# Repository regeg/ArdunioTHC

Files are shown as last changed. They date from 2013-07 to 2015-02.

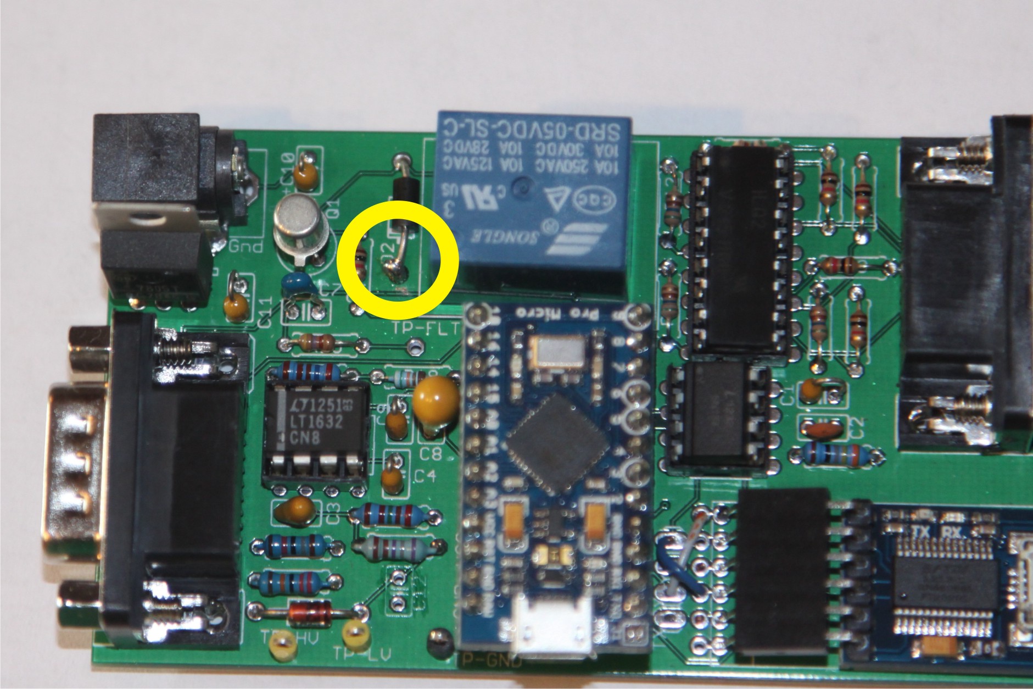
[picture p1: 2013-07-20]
THC Manual/THC Manual/RevE-M top solder bridge.jpg

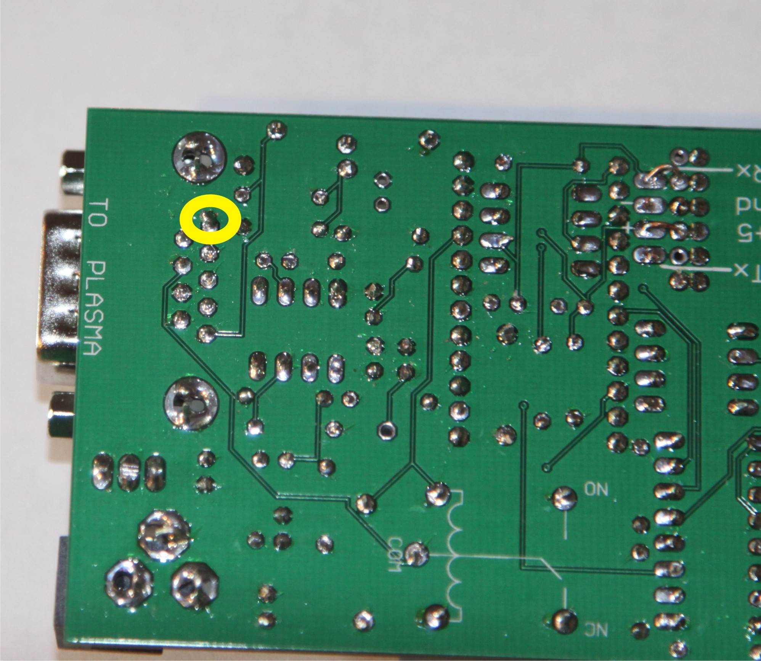
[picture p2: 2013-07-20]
THC Manual/THC Manual/RevE-M bottom Solder Bridge..jpg

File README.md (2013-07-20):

ArdunioTHC
==========

Arduino-based Torch Height Controller for CNC Plasma torch systems

(see "Status.txt" for current project status.)

***

WARNING: CNC systems are inherently dangerous.  Use of this hardware and software is at your own risk.  I am not an expert at CNC systems, THC's or electrical design.  I'm just an embedded software guy who did the hardware design with help from some experienced EE's.

When working with a THC, you're messing with high voltage.  All of the project information is only for use with the acknowledgement and agreement that no statement of safety or appropriateness is offered for any of the information.  Additionally, you take full responsibility for all uses of this hardware, software and documentation.

***

Background
----------
Having recently built a Computer Numeric Control (CNC) driven Plasma torch cutting table, I wanted to add a torch height controller (THC).  I decided to make my own and open source it.

Both the CNC table build and the THC development couldn't have been done without the significant support I received from the folks on the Everlast Forums.  	www.everlastgenerators.com/forums
These are great forums for support with all things welding and plasma cutting.

I have built this THC specifically to work with the Everlast Power Plasma 50 plasma torch.  This is the unit I have and I've been very happy with it.

There are two very significant aspects that make the Everlast PP50 ideal for this project.  They are:
	- Pilot Arc start
	- full CNC interface

Pilot Arc Start - the PP50 offers a "pilot arc" start, this is in contrast to an HF (High Frequency) start.  The HF start is very noisy and has been reported to cause significant interference with computer systems.

Full CNC Interface - all control signals are available on a connector on the back of the PP50.  They are:
	- Torch On (input, dry contact)
	- Arc Good (output, dry contract)
	- Full torch voltage
	- Divided torch voltage

This hardware design uses the full arc voltage.  I've observed about 2 volts of noise on the torch voltage signal, no matter what you use (full voltage or divided voltage).  By using the full voltage and dividing it myself, the noise is kept to a significantly lower percentage of the signal.

I have not tested the THC with any other brand of plasma torch.  It should be a good starting point to make a THC to work with other torches that provide a CNC interface.

Hardware
--------
There are two versions of the shield.  The first is a shield and will work with an Arduino Mega.  This has been the primary platform.  A newly released version uses the Arduino Micro Pro.

The hardware provides:
	- isolated interface to CNC system
	- interface to Power Plasma 50 CNC interface
	- isolated RS-232 (TTL levels) for interface to THC

--

I will be updating all files as the project progresses.  There will be the following subdirectories:
	- "ArduinoSource", using Eclipse plugin from www.baeyens.it/eclipse/
	- "THC Manaul", a users guide to building and use the THC
	- "HardwareDesign", Eagle schematic and PCB layout files
	- "WindowsSource", C# .Net application used to capture cutting data
	- "Mach Plugin", A Mach3 plugin to allow Mach to control the THC

License
-------
This is copyrighted software that is released under the Creative Commons Attribution-NonCommercial-ShareAlike 3.0 license

The unofficial summary is:

You can use it as it is for non-commercial purposes.  If you modify it, you must make the modifications public and attribute the original source to me.

(If you want to license it for commerical use, please contact me.)

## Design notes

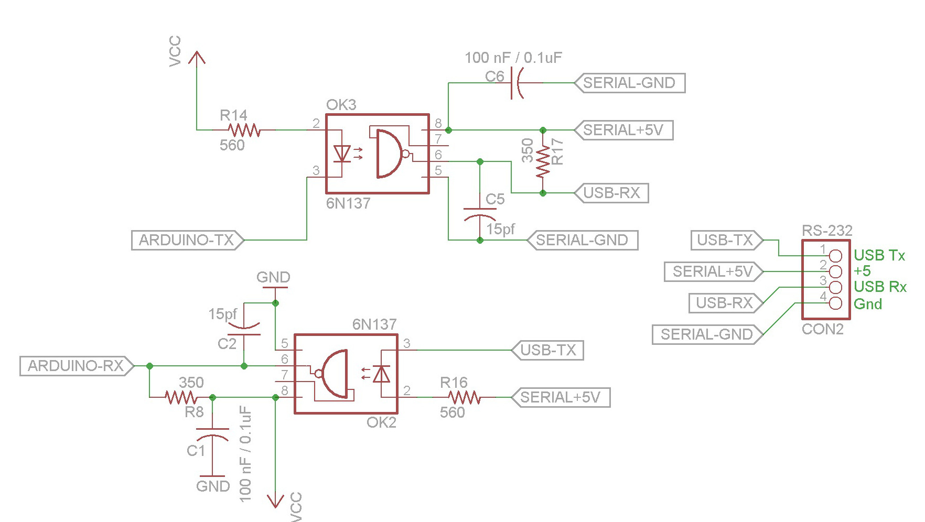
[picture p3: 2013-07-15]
THC Manual/THC Manual/RS-232Schematic.jpg

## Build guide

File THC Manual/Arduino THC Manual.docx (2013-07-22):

For the Everlast Power Plasma 50

User Manual

Open source hardware and software free to non-commercial use.

www.github.com, project: regeg/ArduinoTHC

Revision | Date | Changes
0.1 | 7/11/13 | Initial version w/ pictures and both Shield & Micro
0.2 | 7/20/13 | Added BOM and white wire directions for Micro board
0.3 | 7/22/13 | Added section on programming the Arduino

| This icon denotes a significant piece of information.

| This icon denotes a very important warning.

# 1. CNC/Plasma System Requirements

This THC system was designed with specific requirements in mind. The target requirements are:

- Everlast Power Plasma 50 (PP50) plasma cutter
- Mach3 CNC Driver, licensed version required for THC use

## Everlast Power Plasma 50

The PP50 was selected as the initial plasma system to be supported for two reasons:

- It is a good performing and economical plasma cutter with a CNC port and a pilot arc start
- It’s the cutter I have

One aspect of the PP50 CNC interface is that it includes a 100K ohm resistor on both the + and – poles of the arc voltage signal. This plays a role in determining the voltage divider resistor values. While this THC uses undivided voltage, it is not recommended that it be connected directly to the torch voltages (if the plasma unit has no CNC interface). This would require hardware design changes.

## Mach 3 CNC Driver

The Mach 3 CNC driver application is recommended because:

- It is the configuration the system was designed to use
- The long term goal Is to integrate the THC controller directly into Mach

Mach is not required. A Windows PC application can be used to control the THC.

# 2. User Skill Level Requirements

This system is not intended to be a turn-key system for people who are willing or able to build electronics or compile software source code and download the result.

## Electronics Skills

The following skills are required to be able to build the THC:

- Read a schematic
- Solder (and probably de-solder our mistakes)
- Order, identify and know how to handle discrete electronic components
- The ability to troubleshoot/debug any errors made during assembly of the system

## Software Skills

The following software skills are required to be able to build the THC:

- Install and use the Arduino development environment
- Compile and download an Arduino software project
- Read C/C++ with a very basic understanding to allow “tweaking” of key performance variables

# 3. Theory of Operation

## Torch Voltage Behavior

The way a THC works is very simple. When using a plasma cutter the voltage used to cut will increase and decrease in relation to the height of the torch from the metal surface. (Plasma cutters have constant amperage and variable voltage.) Cutting voltages are typically under 200 volts DC. The PP50 cuts in the range of 90 volts to 120 volts (roughly).

| When the torch goes higher above the cutting surface, the voltage increases. When the torch goes closer to the cutting surface, the voltage decreases.

One volt difference in the cutting voltages translates to about 15 thousandths of an inch. The target voltage to use when cutting is dependent on:

- Metal thickness
- Speed of torch motion

If the torch slows down while cutting (for example: when cutting a corner or changing direction), the distance the arc has to travel will increase. This will result in a higher voltage even though the torch is at the proper height. Since the THC has no way of knowing the speed of the torch, a setting in Mach 3 is used to instruct it to ignore the THC if the speed drops below a user set percentage of the cutting speed.

## Torch Height Controller Functions

The basic function of the THC is very simple. It compares the actual torch cutting voltage to the user set target voltage. If the torch cutting voltage is higher than the target voltage, it signals Mach to move the torch down. If the torch cutting voltage is lower than the target voltage, it signals Mach to move the torch up.

There are lots of special cases and other behaviors that will be described later, but that’s the basics of a THC.

## THC Block Diagram

The following is a high level block diagram of the THC.

As can be seen from the diagram, the fundamental components of the THC hardware are:

- Voltage Monitoring
- Torch On Relay
- RS-232 Opto-Isolator
- CNC Opto-Isolator
- 5 Volt Voltage Regulator

The “Voltage Monitoring” consists of:

    - Voltage divider
    - High frequency op-amp filter
    - Low frequency Resistor-Capacitor (RC) filter

As seen, there are three different interfaces. They are:

- Plasma Inteface
  - Torch On Output
  - Arc Good Input
  - Torch Voltage Input
- CNC Interface
  - Torch On Signal (input from CNC)
  - Arc Good Signal (output to CNC)
  - Torch Up Signal (output to CNC)
  - Torch Down Signal (output to CNC)
- Serial Control Interface (bi-directonal RS-232)

## THC Interfaces

### Torch On Interface

To use a THC you must have the ability to turn the torch on and off under computer control. This is typically not a digital interface. Generally plasma cutters require a relay (sometimes referred to as dry contacts) to close a circuit to turn the torch on, and open it to turn the torch off.

The torch on circuit uses a transistor to boost the output of an Arduino DigitalOut to sufficient current to control the relay. The relay circuit is connected directly to the Normally Open (NO) contacts of the relay.

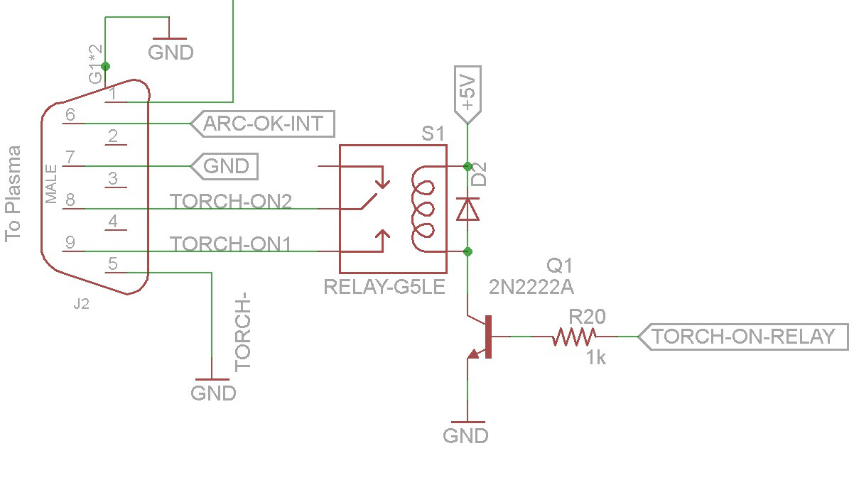
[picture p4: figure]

### Arc Okay Signal

To use a THC the CNC system must know when the cutting arc is good so that it can start cutting. If, while cutting, the arc okay signal goes away, the CNC will stop motion.

The arc okay signal on the plasma is typically a relay (dry contact). To read this, an Arduino DigitalInput is connected to one of the two arc okay signals, and the ground from the Arduino is connected to the other.

The Arduino input is “tied high”. This means that it will read 5 volts if there is nothing connected to it. So, when the plasma closes the relay, the ground is connected to the input and it changes from 5 volts to 0 volts. This is commonly referred to as an “active low” signal.

| Electrical noise, or interference, can cause voltages to show up in places they wouldn’t normally be. If you have a signal configured for “active high”, or to go on when there is voltage present, electrical noise can cause a false signal to occur.

| This is a big safety issue. You should always use “active low” to avoid a situation where the system is stopped and you’re in the process of working around the area of the torch and electrical noise causes it to turn on unexpectedly.

### Plasma Voltage Interface

The plasma voltage interface is the most complex of all the electronics.

#### A Word on Electrical Isolation

Electrical isolation is having subsystems that interconnect that do not share a common ground. This prevents the transmission of noise between systems and the chance of unexpected voltages that can damage components/systems (ground loops).

Addressing grounds loops and isolation can be very complex. I took a very simple approach:

- the interface signals to the CNC are opto-isolated
- the USB/RS-232 interface to the PC is opto-isolated
- the Arduino is powered by a two-prong wall wart and the board is not tied to the common or A/C ground

Because the CNC system and the PC are opto-isolated, they cannot be damaged by problems with the torch or THC. I believe this approach isolates the THC sufficiently, bug I figured that if I was wrong the worst I could do is fry an Arduino and THC board (which relatively cheap to replace).

| This worked for me, but I’m not an electrical engineer and it may not be the best way to do this. It was very easy though.

#### A Word on Plasma Torch Voltage Polarity

Plasma torches use a negative voltage to cut. The ground clamp is at 0 volts and the torch is at -120 volts (or whatever). If you take a battery powered volt meter (isolated from the plasma’s ground) and connect the negative lead to ground and the positive lead to the torch, you’ll see a negative voltage.

However, if you connect the positive lead to ground and a negative lead to the torch – you see a positive voltage.

If the CNC port on the plasma unit provides an isolated output (I don’t know if the PP50 output is isolated), or if you provide isolation by some other means, you can just read the voltage normally by swapping polarities.

#### Plasma Torch Voltage Dividers

The cutting voltage used as an input is a full voltage signal (up to 200 volts) with the potential for lots of electrical noise on it. This signal has to be dropped to a level the Arduino can read without being damaged (0 to 5 volts). Additionally, electrical noise on the signal must be reduced/removed.

The PP50 does provide a divided voltage signal that can either be 1/16th or 1/50th of the voltage. The following table shows how this works:

Torch Voltages and Dividers

Actual Voltage | Divider | Output Voltage
120 volts | None | 120 volts
120 volts | 1/16th | 7.5 volts
120 volts | 1/50th | 2.4 volts

What I had found in my testing is that I had about 2 volts of noise on the plasma signal. What this means is that no matter what voltage output is used, an extra two volts will be added on top of it.

If using the 1/16th divider the added noise would be more than 25% of the signal, if using the 1/50th divider the added noise would be almost as much as the signal. For this reason, the full voltage is used so that when it is divided down, the noise is divided down with it.

#### Voltage Divider

A simple voltage divider is used to step the voltage down from the cutting range to a maximum of 5 volts. While the torch voltage is specified to be up to 200 volts, in practice I have not seen a voltage greater than about 130 while cutting. As a result, I targeted a voltage divider value for a lower input voltage.

This gives better voltage resolution, but can result in the voltage input exceeded 5 volts and damaging the electronics. To address this, a Zener Diode is incorporated in the circuit to ensure the voltage does not exceed 5 volts.

C12 is a “spare” capacitor that I put in to make it easier to experiment with different filtering arrangements. The “TP-“ symbols are for optional Test Point connectors. These allow easy monitoring of voltages. “TP-HV” is for High Voltage (full torch voltage) and “TP-LV” is for the low voltage (divided and unfiltered voltage) , TP-FLT is for the final filtered voltage and TG-GND is for the ground.

The voltage divider circuit with Zener diode is shown below.

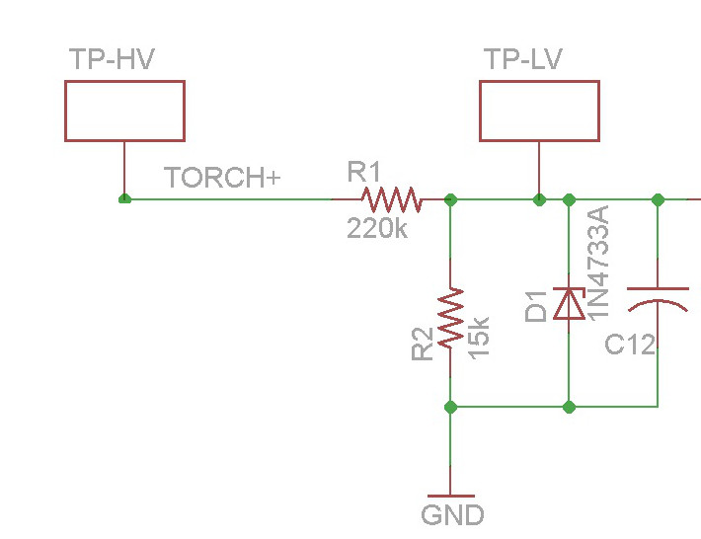
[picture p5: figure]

| For the PP-50 the value for R2 in the diagram above can bet either 15K or 18K. 15K Ohms will give 7 counts for volt. 18K Ohms will give almost 8 counts per volt. 18K will give better resolution, but less voltage range.

The voltage reduction is determined by the following formula:

VOut = ( (R1) / (R1+R2) ) / VIn

So, for a 100 volt input, the formula would be:

VOut = ( 15,000 / (220,000 + 15,000) ) * 100

VOut = 0.06383 * 100

VOut = 6.383 Volts

NOTE: one thing to keep in mind is that the 100K ohm resistors on both the positive and negative legs of the voltage signal change the voltage that the circuit sees.

So, a 120 volt cutting voltage is seen as (XX) volts at the CNC port and the voltage divider. The voltage divider results in this being changed to (XX) volts at the output of the voltage divider.

The Arduino has a 10 bit Analog to Digital converter. This means that a 0 volt signal is seen as 0 “counts” and a 5 volt signal is seen as 1023 “counts”.

This results in the following formula to convert cutting voltage to analog counts (keep in mind that the tolerance, or accuracy, of the resistor adds a bit of slop to this calculation).

(insert overall formula)

So, the output of the voltage divider, along with all its noise is passed to the high frequency op amp filter.

#### High Frequency Op Amp Filter

Using an oscilloscope I found that the environment was fairly noisy. The noise seemed to be mostly from the PC (older commercial PC). Because that was there to start with, I didn’t pursue it further to see what each component of the system (steppers, stepper drivers, plasma) introduced.

The op-amp filter was designed using Texas Instruments free filter design application “FilterProDesktop”. A friend who is an electrical engineer advised on the optimum values to use.

Op-Amp selection is critical. While none is specified in the schematic, I started with a TI part that was a general purpose rail-to-rail op-amp. This resulted in never went below 1.8 volts and never exceeded 3.8 volts. Using a Linear Technologies op-amp that had almost the same specifics I got satisfactory results.

Other op-amps can be explored (the op-amp selected is around $7), but I did not do that since I had something that worked.

It’s worth noting that Analog Device’s circuit simulator (LTSpice) is an excellent tool for examining the behavior of circuits. I used this extensively to understand and tune the circuit design. It also helped me identify an op-amp that would work.

#### Low Frequency RC Filter

The op-amp filter will filter frequencies above (1K hz?). When examining the actual output of the filter there was a significant 60 hz noise component.

To remove the 60 hz noise I used an RC filter. It’s important to understand the difference between the (filter frequency) and the (stop band frequency).

The (filter frequency) (is the frequency at which the filter function starts to affect the signal.

The (stop band frequency) is the frequency at which all signals above that are filtered out.

To filter out 60 hz noise, the (filter frequency) must be significantly lower than 60 hz. However, the lower frequency that the filter is, the slower the signal will show changes. If there is too much delay, you won’t be able to do accurate torch height control.

A good RC Low Pass Filter design tool can be found at: http://sim.okawa-denshi.jp/en/CRlowkeisan.htm

The schematic and formula for calculating the filter frequency are shown below:

Using the calculator and experimenting with different filter cut off frequencies, I ended up with an optimum value of 470 ohm resistor and 68 uF capacitor. The response chart for this is shown below.

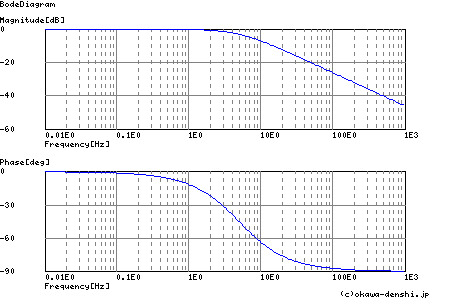
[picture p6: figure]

In the first graph above, 1E0 indicates 0 Hz and, 10E0 is 10 Hz, etc.

The values used were a trade-off of noise reduction and signal response. The filter can be adjusted for an optimum behavior based on your goals. I wanted a fairly fast response so that I could detect when the torch was crossing a kerf (already cut area) to disable torch height control. This prevents the torch from being sent lower and “crashing’ into the metal at the other side of the kerf.

## CNC Interfaces

The CNC interfaces are straight-forward. There is one input signal to the THC and three output signals. These are all opto-isolated. For opto-isolation, the CNC must provide it’s 5 volt supply to power the opto-isolator.

## Serial Command Interface

The initial design of the THC was “stand-alone”. It had push buttons and a 2 line LCD display. There were a number of issues with this:

- There was no way to capture the cutting voltages (needed to develop and debug the control algorithms)
- The LCD library seemed to have some performance issues
- Wiring the buttons was a rat’s nest
- The THC was controlled by its interface, but it was near the plasma/CNC but the system was controlled by the PC’s screen and keyboard (it was very difficult to interact with both)

As a result, I dumped the LCD/button interface and whet to a high speed serial interface. (The original source code is available is anyone wants to pursue that approach.)

The Arduino provides TTL level serial data signals, not RS-232 levels. This allows the signals to be opto-isolated. However, the other size must provide power for its opto-isolators and level conversion from TTL to RS-232. I did this by using a cheap (FTDI) TTL to USB converter purchased from E-bay ($3).

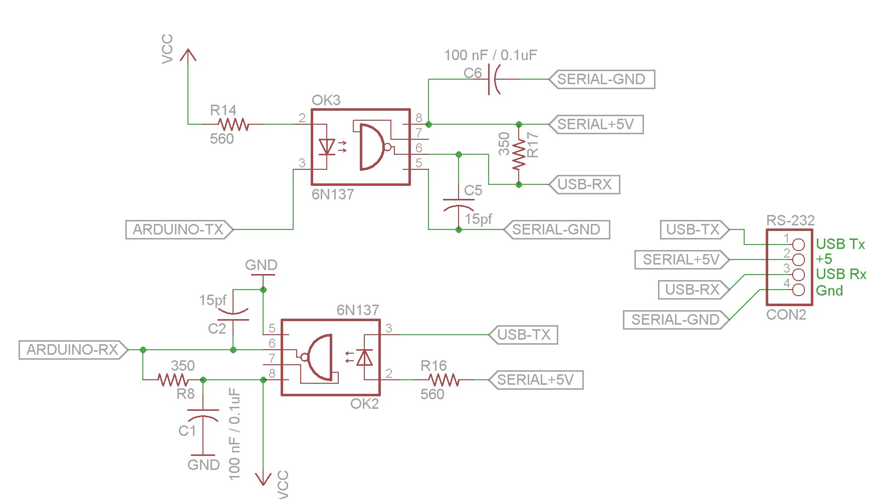
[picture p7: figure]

| The serial cable must be shielded or the noise will make the system inoperative.

## Power Supply Subsystem

An Arduino-compatible power input jack and voltage regulator are provided on the board. These are not necessary as the power can be provided by the Arduino. I put these on the board so that in the future I could move the THC to a Freescale Freedom board, which does not have a wall-wart connector.

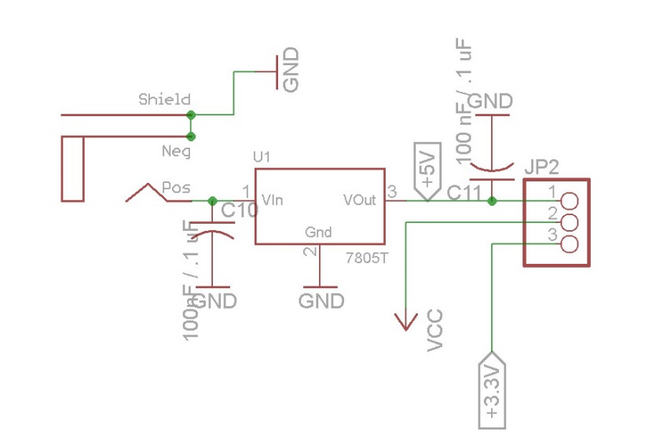
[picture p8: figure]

## Arduino

I started the development with an Arduino Mega. I selected this processor because it is one of the fastest of the Atmel Arduinos (16 MHz) and had the most program (flash) and data (RAM) space.

Once the LCD was removed and the library was no longer needed, the memory requirements dropped significantly. The THC will now work with an UNO – but that has not been tested.

An Arduino Micro Pro version has also developed. The Arduino Micro Pro must be a 5 volt version. The 3 volt version is not currently supported.

# 4. THC Boards

There are two versions of the THC. One is a shield style “S” and one uses a Micro Pro “M”.

The schematics and board layouts are at the end of this document.

The schematics and board layouts were done using EagleSoft CAD. There is a free version available that will allow you to open and examine both the schematic and the board layout. You can also generate a Bill Of Materials (BOM) that is a list of all parts necessary.

The design assumes that all capacitors are non-polarized. However, the capacitor for he RC voltage filter is marked with a + side in the event you use a polarized capacitor (i.e. tantalum or electrolytic).

| The power inlet jack, voltage regulator and associated capacitor are optional and are not needed for normal use with an Arduino system.

| The test points are optional but assist in reading voltages or taking scope captures during operation.

| Sockets for all IC’s are optional, but reduce the chance of heat damage when soldering and allow easier insertion and removal/replacement.

Below are the completed THC’s. The top board in the image is the “Shield” version of the THC and it is mounted on an Arduino Mega board (the purple is a board protector made with a 3D printer). The bottom board in the image below is the “Micro” version of the THC.

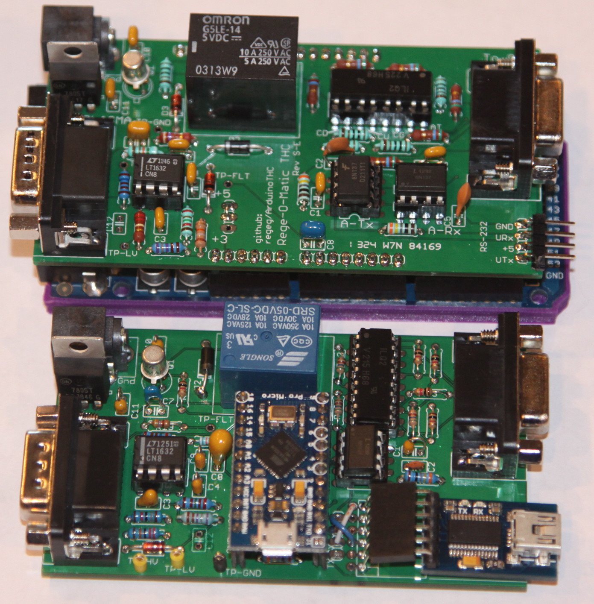
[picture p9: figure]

## Connecting to the Plasma

The board is designed to use right angle mount DB-9 connectors to provide for ease of connection and disconnection. If you choose, you can wire your cables directly to the board.

You must use shielded wire. And using a ferrite wouldn’t be a bad idea. (I connected the shield to the case of the Plasma Unit but left it unconnected on the THC side).

If you use the DB-9, the signals are located as shown.

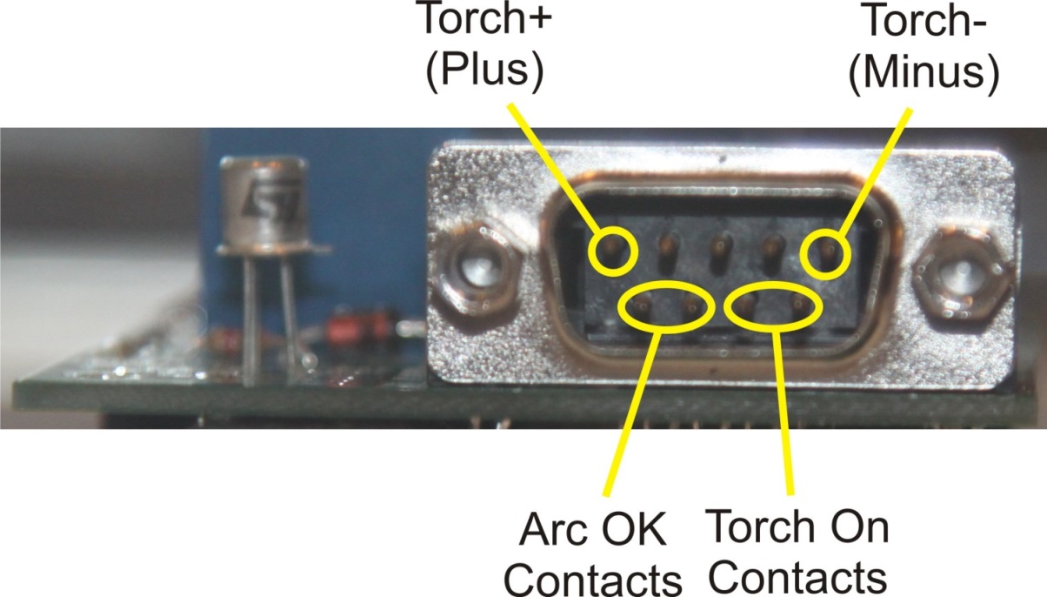
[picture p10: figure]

## Connecting to the CNC

The board is designed to use right angle mount DB-9 connectors to provide for ease of connection and disconnection. If you choose, you can wire your cables directly to the board.

You must use shielded wire. And using a ferrite wouldn’t be a bad idea. (I connected the shield to the case of the Plasma Unit but left it unconnected on the THC side).

If you use the DB-9, the signals are located as shown, if you are looking at the connector from the side the cable attaches to.

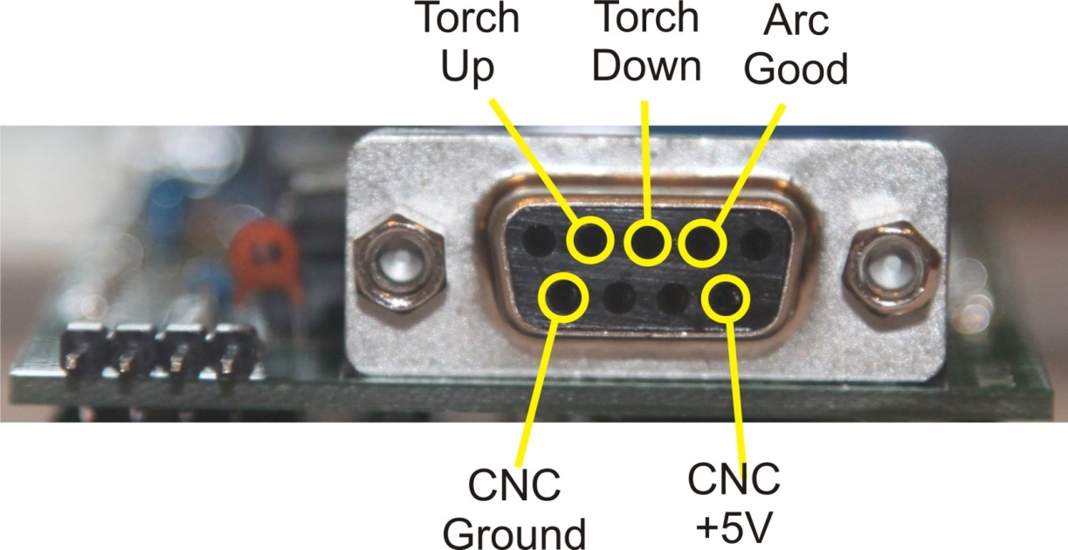
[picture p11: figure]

| The CNC must provide the 5 volt supply to operate the opto-isolators.

## Connecting the Serial Port - Shield

The board is designed to use right angle .1” pin connectors (standard on the Arduino). However, you can solder your serial cable directly to the board.

You must use shielded wire. In my system I used shielded wire but did not need to connect the shield to anything. (Without the shielded wire there was too much noise for reliable data communication.)

NOTE: the PC/level converter must provide the 5 volt supply to operate the opto-isolators.

## Connecting the Serial Port – Micro

I used head pin sockets with extra long pings (the sockets used on shields with long pins to go into the Arduino board) and bent the legs. This is then used to plug the RS-232 to USB adapter into.

Since there are multiple configurations of RS-232 to USB adapters, all with different pin-outs, you must put jumpers in to connect the board signals to the adapter signals (+5, Gnd, Rx, Tx).

# 5. Board Assembly

The following is the suggested order of assembly. While any order will work, after building multiple versions of the prototypes, I found this sequence to be easiest.

## Shield

1) Resistors
2) Diodes
3) 5 volt jumper (See below)
4) IC sockets (if desired)
5) Test points (if desired)
6) DB-9’s
7) Right angle header pin for serial to USB (best to solder from the top of the board)
8) Power inlet (if desired)
9) Header pins (This is best done by putting them in an Arduino board and placing the shield on top. Solder one pin on each end of each header. Then remove the shield from the Arduino board and solder the rest of the pins)
10) Relay
11) Voltage Regulator (if desired)
12) Transistor
13) Capacitors

Step 3: The shield was designed so that it could be used with a 3V Arduino or Arduino compatible board (Freescale Freedom). This has not been tested! However, for the board to work – you must put a jumper between the center and +5V pad as shown in the drawing.

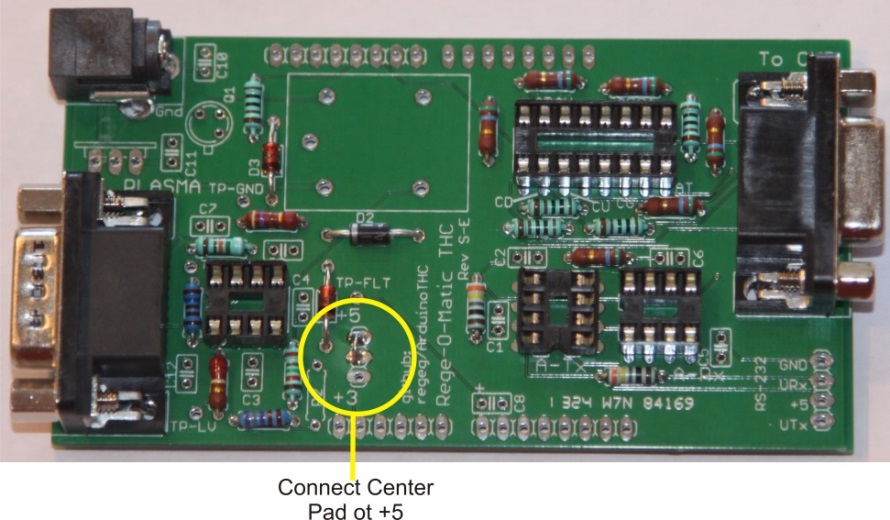
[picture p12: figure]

In the photo below you can see how the bottom side of the components of the power circuit contact the outside shield of the USB connector.

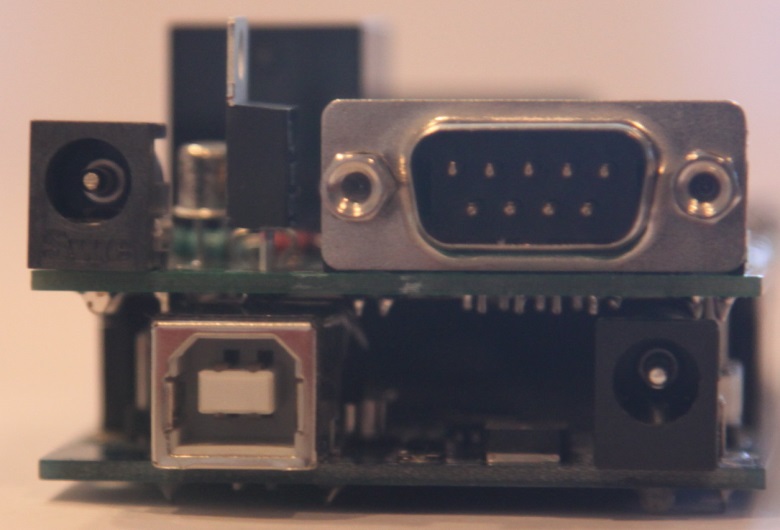
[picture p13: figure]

| DON’T FRY YOUR BOARD! One drawback of the design is that there are soldered connections that come in contact with the metal shield on the Arduino’s USB port. You will reduce this if you don’t build the power supply portion of the board. In either case (building the power supply or not) you should cover the USB shield in at least 2 or 3 layers of electrical tape.

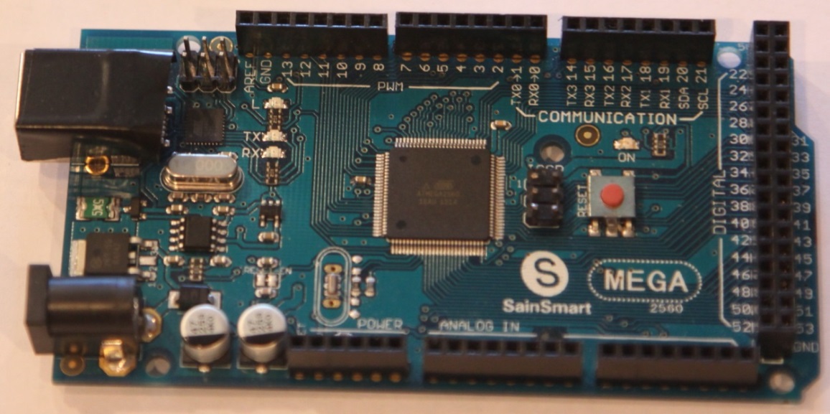
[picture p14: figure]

## Rev E-M Required Modifications / White Wires

The design has gone through many iterations but the Rev E version introduced the Micro design. As a result of being the first pass, there are two missing connections that require additional work for proper operation.

### Torch Voltage (-) Not Tied to Ground

At the DB-9 connector to the plasma unit, the Torch Voltage (-) signal is not tied to ground. The bottom copper plane of the board (all copper areas that are not traces) is a ground plane. The input signal can be connected to that by carefully scraping the solder mask away to allow soldering to the copper underneath. Alternately, you can run a wire from the DB-9 pin to another pin wired to ground.

The picture below shows the bottom of the board where solder mask was removed from the ground plane and a solder bridge was added between the ground plane and the pin.

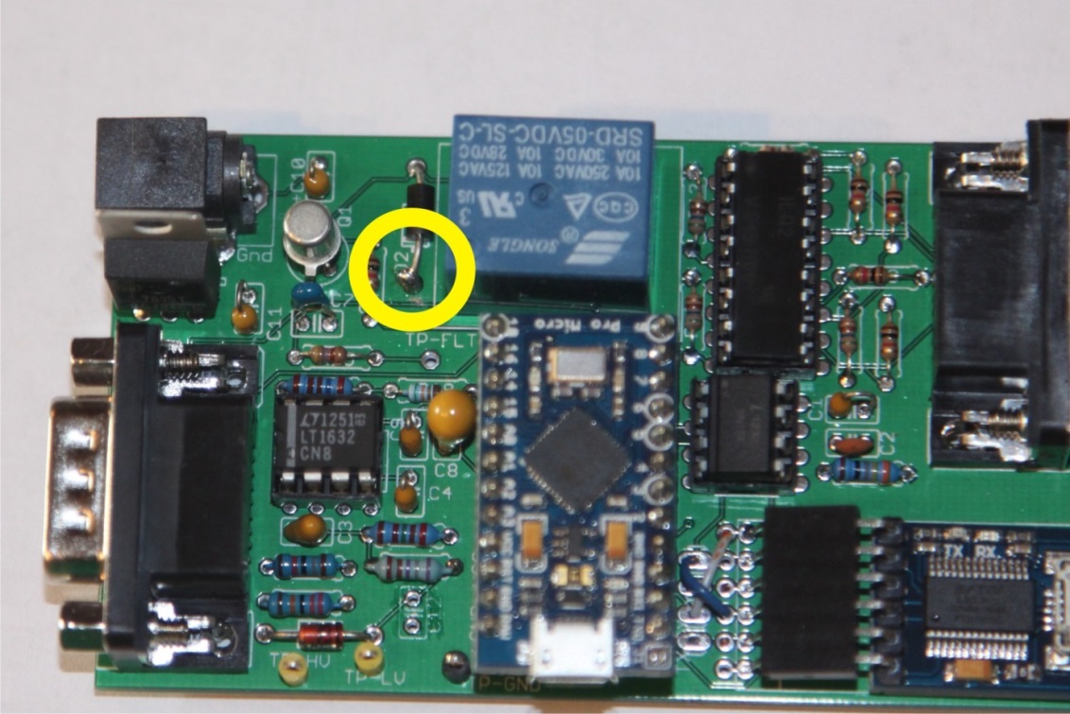
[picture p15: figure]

### +5 Volts Not Tied Relay and Arduino Micro Module

The Arduino Micro module was built to be single voltage (+5 volts) only. When the jumper was removed one net that connects the diode on the torch-on relay and the +5 volt supply to the Arduino Micro was not connected to the +5 volt supply.

The top copper plane of the board (all copper areas that are not traces) is a +5 volt plane. The net connecting the diode and Micro can be connected to +5 volts by carefully scraping the solder mask away to allow soldering to the copper underneath. Alternately, you can run a wire from the diode to a +5 pin.

The picture below shows the top of the board where solder mask was removed from the ground plane and a solder bridge was added between the +5 volt plane and the diode.

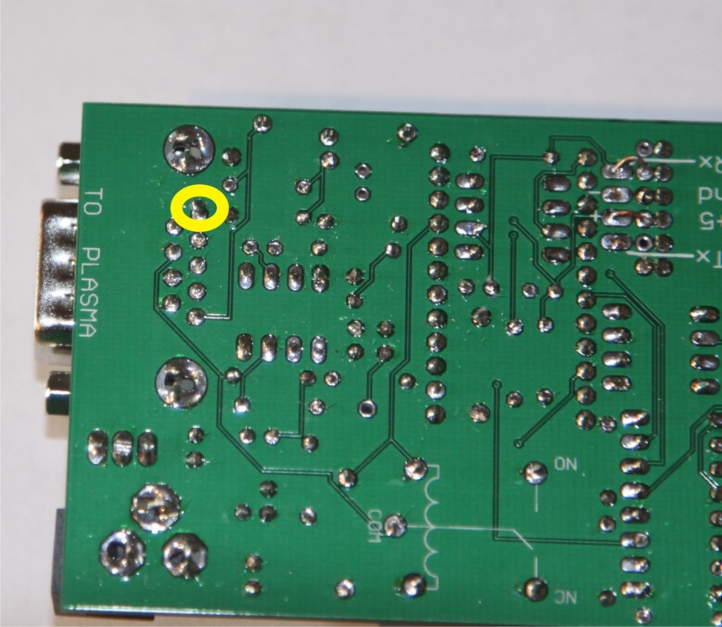
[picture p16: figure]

# 6. Board Checkout

If you build the board properly, it should all just work. That probably won’t be the case, so you’ll need to troubleshoot your hardware. Trouble shooting is beyond the scope of this manual, but the following order is suggested.

1. If you build the power supply, without plugging in the Arduino, power up the shield and measure voltages to ensure it is operating correctly.
2. Program the Arudino
3. Get the serial port working
4. Test the relay
5. Test the CNC connections
6. Test the Plasma connections

## Program the Arduino

You need to program the Arduino with the most current source code. When no THC is connected and the Arduino is running the THC software, you should see the serial port LED flashing regularly.

Remove power and connect the THC. Use the wall-wart to provide power. Verify that the serial port LED is flashing. If all LED’s go off – you have +5 shorted to ground somewhere on your board.

NOTE: When running the Arduino with the THC attached, you must use a wall-wart for power. Using the USB to power the system will prevent the serial port from operating properly and can cause a ground loop that can destroy your computer.

## Get the Serial Port Working

By getting the serial port working first, you can use the stand-alone windows application to ensure the system is running and debug the connections to the Plasma and CNC. If it stand-alone app doesn’t work right away, you may want to use a terminal program to send characters and look at what’s received as you’re debugging (TeraTerm is a good choice).

## Test the Plasma Connections

Once the serial port is working the stand-alone Windows app can be used to test the Plasma connections.

Before connecting the torch, make sure the relay clicks on and off when commanded from the Windows app.

Next, short the two Arc Good signals and verify that the signal status on the Windows app is updated appropriately.

| Make sure the torch is anchored in a safe location before attempting to turn it on.

NOTE: You may need to turn the torch on frequently and run it on pilot arc for a while to debug. This is very hard on consumables. If you have old crappy consumables – they are good to use for this.

Once you know that the relay works and the Arc Good work, connect the torch and verify it turns on and off when the relay is flipped.

If the torch control is working you should see the voltage display updated. If it is not, you need to run the torch while debugging the voltage divider and filter circuits.

| You will be debugging a circuit that can have up to 200 volts on it. Be careful.

## Test the CNC Connections

| The CNC connections should initially be debugged with the plasma disconnected.

First, use the test capability of the Windows app to generate the Arc Good, Torch Up and Torch Down signals. You can use the “Diagnostics” screen in Mach to verify if they are working correctly.

If they are not, it can either be a problem with your board and/or cables or with your Mach configuration. Double check connection of your CNC output signals to the pins on the Break Out Board (BOB) and verify that is how the “Outputs” are configured in Mach.

The main screen of the default plasma screen set in Mach provides the ability to turn the torch on and off. You can use this and monitor the signal status on the Windows app to see if this signal is correct.

# 7. Programming the Arduino

## Download the Arduino Tool Set

The Arduino compiler and tool set are constantly being updated. The currently supported version is 1.05. The software should work on new versions, but changes in the compiler can sometimes cause compile errors that require minor changes.

To download the Arduino tool set:

1) Go to www.arduino.cc
2) Click the “Download” label in the top title bar
3) You can use either the “Windows Installer” or the “Windows (ZIP File)”.
  a. If you use the “Windows Installed”, run the program after downloading
  b. If you use the “Windows ZIP file”, open the file after downloading and copy to a convenient location (usually “C:\Arduino-1.0.5” (or something similar)

Run the Arduino IDE and make sure it works.

If you’ve not used the Arduino before, try some of the example software to get the hang of the software and downloading.

## Download the Source Code

To build the software and load it on the Arduino, you need to have the source code. All source code is maintained on GitHub (www.github.com).

1) Go to the Git Hub site
2) Enter “regeg/ArduinoTHC” in the search box on the top menu bard of the window.

| The Git hub name you search on is case sensitive! You must match the case: “regeg/ArduinoTHC”

3) Once the project page comes up, click the “Download ZIP” on the right size of the page.
4) Save the ZIP file somewhere convenient
5) Open the zip file and copy the directories to a convenient location

## Building and Downloading the Source Code

Now that you have the source code downloaded, you must build it and program the Arduino.

1) Start the Arduino development environment
2) Enter the “ArduinoTHC” directory (in the location you previously downloaded it)
3) Enter the “ArduinoSource” Directory
4) Enter the “THC_REV-EM sketch”
5) Open the “THC_sketch.ino” file
6) The project should now be opened with a number of tabs across the top (all the files in the project)
7) Select the “Platform.h” file.
8) Set the “define” for the hardware you are using
  a. If you are using an Arduino Micro Pro, make sure the line with “#define MICRO_THC” IS NOT commented out (a “//” denotes a comment
  b. If you are using an Arduino Mega, make sure the line with “#deifne MICRO_THC” IS commented out.
9) Plug in your Arduino (if using an Arduino Mega, unplug the shield before programming)
10) Select the “Board” Menu
11) Select the board type you are using, either
  a. Arduino Mega 2560, or
  b. Arduino Leonardo (for the Micro Pro)
12) Select the serial port that the board is on
13) In the tool bar, click the icon with a check mark. The software should compile without errors.
14) Click the icon with the arrow pointing to the right to download the code to the board

Once programmed successfully, you should be ready to go.

# 8. First Operational Test

For the first operational test of the THC, you should set the THC to “Bypass” mode. This should allow the system to make cuts without any THC control. While cutting you should verify that the signal statuses are updated (Torch On, Arc Good, Torch Up, Torch Down), the voltage is updated and the system properly cuts material.

# 9. THC Operation

The THC software provides for four modes of operation. They are shown in the state diagram below.

(put in state diagram)

It should be noted that mode changes are not possible when the Torch On or Arc Good signal are active (except for Cruise Mode to Enabled Mode).

## Disabled Mode

Disabled mode will not pass any control signals through so the plasma torch will be non-operational.

| DO NOT use Disabled Mode as an alternative to turning the plasma off while working on the system.

The only way to exit Disabled Mode is through the mode change button.

## Bypass Mode

Bypass mode will pass all signals through to allow cutting and will display cutting voltage. However, it will not perform any torch height control.

The only way to exit Bypass Mode is through the mode change button.

## Cruise Mode

Cruise mode will pass all signals through to allow cutting. When commanded to “go”, the system will go into Enabled mode and start height control using the actual voltage when the “go” command is received as the target voltage.

This mode is intended to be used with a touch-and-go torch holder when cutting a new material and you don’t know the desired cut voltage. The idea is that the touch-and-go controller gets the torch to the right height and once you verify that, you can have it control the height based on that initial cut height.

The Cruise Mode can be exited by the mode change button, or using the “go” command while cutting.

## Operating Mode

This is the normal mode for cutting with torch height control. Within the Operating Mode, there are two states. They are:

- Enabled
- Cutting

Enabled means that the system is ready to cut, but idle.

Cutting is entered once the Torch On signal is received from the CNC and left when Torch On and Arc Good are no longer active.

# 10. Shield Schematic

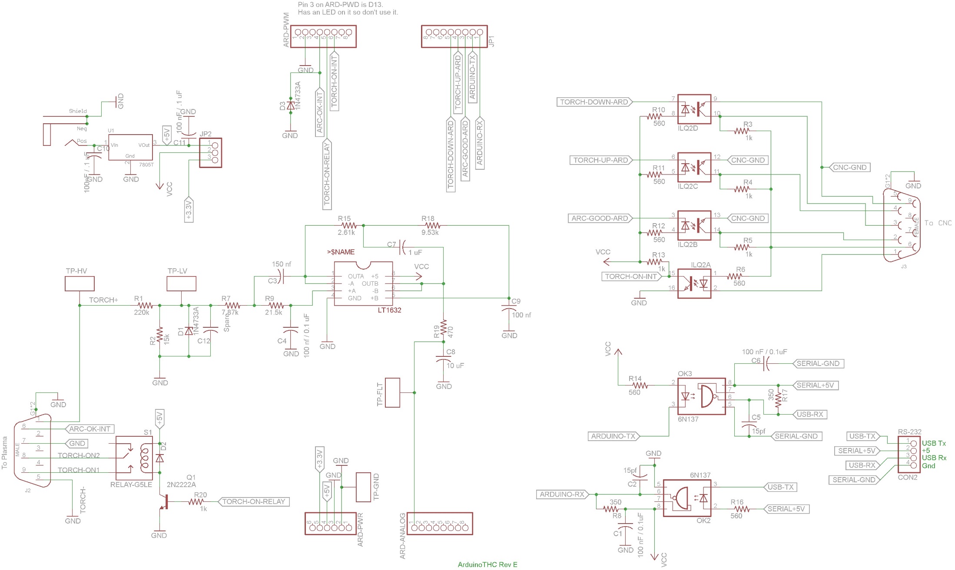
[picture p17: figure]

# 11. Shield Layout

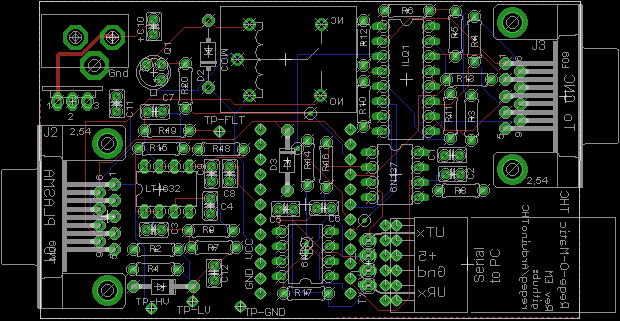
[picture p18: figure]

# 12. Micro Schematic

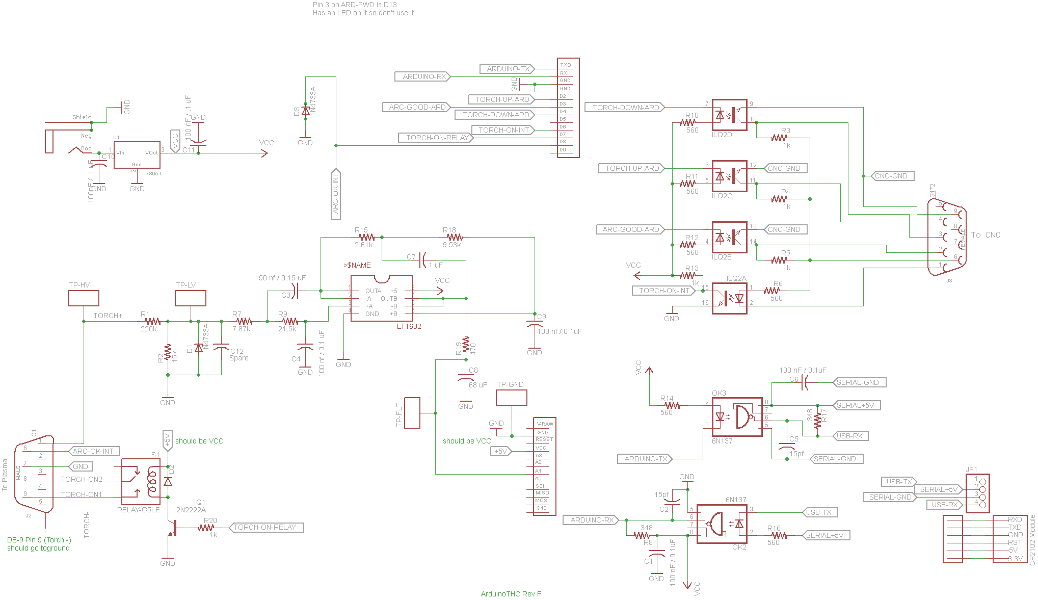
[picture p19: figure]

# 13. Micro Layout

# 14. Bill Of Materials / Parts List

The following is a parts list (Bill Of Materials) that covers both the Shield and the Micro version. The specified part numbers are meant as a guide only.

Headers (Male & Female)
Count | Part | Value | Part Number | Unit Cost | Description | | Price | | Notes
1 | RS-232 Connector | 1x4 Pin Header | | | 0.1" Male Header - Right Angle | | | | Shield Only
1 | ARD-PWR | 1x6 Pin Header | | | 0.1" Male Header - PCB mount, Straight | | | | Shield Only
3 | ANALOG, PWM, JP2 | 1x8 Pin Header | | | 0.1" Male Header - PCB mount, Straight | | | | Shield Only
2 | Arduino Micro Connector | 1x20 | | | 0.1" Female Header/Socket | | | | Micro Only
1 | USB Module Header | 1x6 | | | 0.1" Female Right angle, or 0.1" Long Pin Female Header | | | | Micro Only
Capacitors | | | | | Note: 2.5 mm spacing ideal (not all caps are that spacing
Count | Part | Value | Part Number | Unit Cost | Description | Price | | Notes
4 | C1, C4, C6, C9 | 100 nF / 0.1uF | 399-9785-ND | $0.24 | Capacitor | $0.96
2 | C2, C5 | 15pf | DigiKey: 1427PH-ND | $0.30 | Capacitor | $0.60
1 | C3 | 150 nf / 0.15uF | 399-4278-ND | $0.36 | Capacitor | $0.36
1 | C7 | 1 uF | 478-7666-ND | $0.73 | Capacitor | $0.73
1 | C8 | 68 uF | 445-8249-ND | $0.86 | Capacitor | $0.86
Diodes & Transistor
Count | Part | Value | Part Number | Unit Cost | Description | Price | | Notes
2 | D1, D3 | 1N4733A | 1N4733AFS-ND | $0.23 | Zener Diode | $0.46
1 | D2 | 1N4001 | 1N4001-E3/54GICT-ND | $0.48 | Diode | $0.48
1 | Q1 | 2N2222A | 497-2598-ND | $1.26 | NPN Transistor | $1.26
IC's and Sockets
Count | Part | Value | Part Number | Unit Cost | Description | Price | | Notes
1 | ILQ2 | ILQ1 | 751-1330-5-ND | $2.47 | 4 Channel Opto-Isolator | $2.47
2 | OK2 | 6N137 | 160-1791-ND | $0.90 | 1 Channel Opto-Isolator | $1.80
1 | U$1 | LT1632 | LT1632CN8#PBF-ND | $6.66 | Opamp | $6.66
1 | Socket for ILQ2 | | | | 12 Pin DIP IC Socket | | | Optional, but recommended
3 | Socket for Optos & Op Amp | | | | 8 Pin DIP IC Socket | | | Optional, but recommended
DB-9 Connectors
Count | Part | Value | Part Number | Unit Cost | Description | Price | | Notes
1 | J2 | DB9-MALE | 609-4003-ND | $0.95 | DB9M-RIGHT-ANGLE | $0.95 | | Can wire directly instead of using a connector
1 | J3 | DB9-FEMALE | 609-4009-ND | $0.95 | DB9F-RIGHT-ANGLE | $0.95 | | Can wire directly instead of using a connector
Resistors
Count | Part | Value | Part Number | Unit Cost | Description | Price | | Notes
5 | R3, R4, R5, R13, R20 | 1k | PPC1.00KYCT-ND | $0.26 | Resistor | $1.30 | | resistors 6.5mm x 2.5mm
2 | R8, R17 | 348 | PPC348YCT-ND | $0.26 | Resistor | $0.52
1 | R19 | 470 | PPC470W-1CT-ND | $0.37 | Resistor | $0.37
6 | R6, R10, R11, R12, R14, R16 | 560 | PPC560W-1CT-ND | $0.37 | Resistor | $2.22
1 | R15 | 2.61k | 2.61KXBK-ND | $0.10 | Resistor | $0.10
1 | R7 | 7.87k | 7.78KXBK-ND | $0.10 | Resistor | $0.10
1 | R18 | 9.53k | PPC9.53KYCT-ND | $0.26 | Resistor | $0.26
1 | R2 | 15k | PPC15.0KYCT-ND | $0.26 | Resistor | $0.26 | | Alternate 18k / S18KHCT-ND
1 | R1 | 220k | PPC220KW-1CT-ND | $0.37 | Resistor | $0.37
1 | R9 | 21.5k | PPC21.5KYCT-ND | $0.26 | Resistor | $0.26
Relay
Count | Part | Value | Part Number | Unit Cost | Description | Price | | Notes
1 | S1 | RELAY-G5LE | Z1011-ND | $1.48 | Relay | $1.48
| | | | | Total (for priced parts above) | $25.78
Optional - Shield or Micro
Count | Part | Value | Part Number | Unit Cost | Description | Price | | Notes
4 | TP-FLT, GND, HL, LV | TEST-POINT-.040-HOLE | 5001K-ND | $0.33 | Test Point | $1.32
Required on Mirco / Optional on Shield
Count | Part | Value | Part Number | Unit Cost | Description | Price | | Notes
1 | J1 | N/A | SC1313-ND | $1.57 | 2.1MM-PLUG | $1.57
1 | U1 | N/A | NCP7805TGOS-ND | $0.46 | 7805T Linear voltage regulator | $0.46
2 | C10,C11 | 100 nF / 0.1uF | 399-9785-ND | $0.24 | Capacitor | $0.48
0 | C12 | N/A | N/A | $0.00 | Capacitor, Unused | $0.00
Shield Only - Optional
Count | Part | Value | Part Number | Unit Cost | Description | Price | | Notes
| JP2 | 0.1" Pin Header | | | PINHD-1X3 Voltage jumper
| for JP2 | 0.1" Jump | | | Jumper

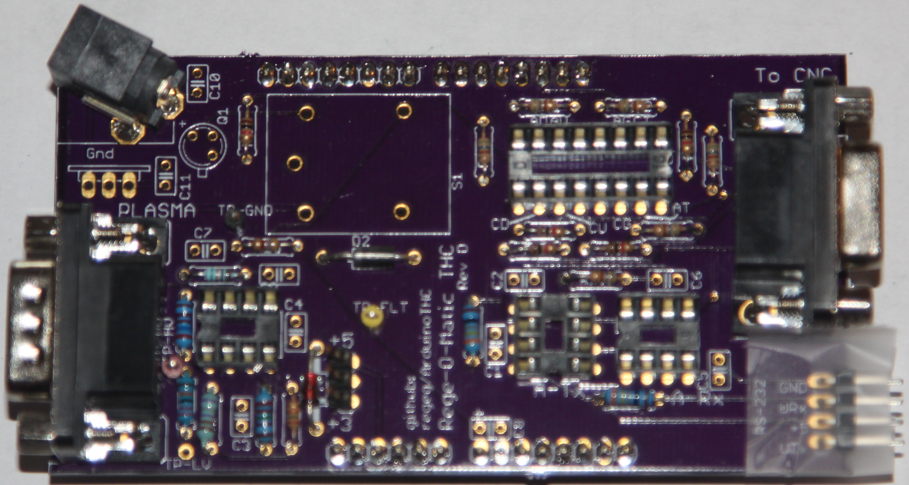
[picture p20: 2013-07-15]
THC Manual/THC Manual/RS232Connector.JPG

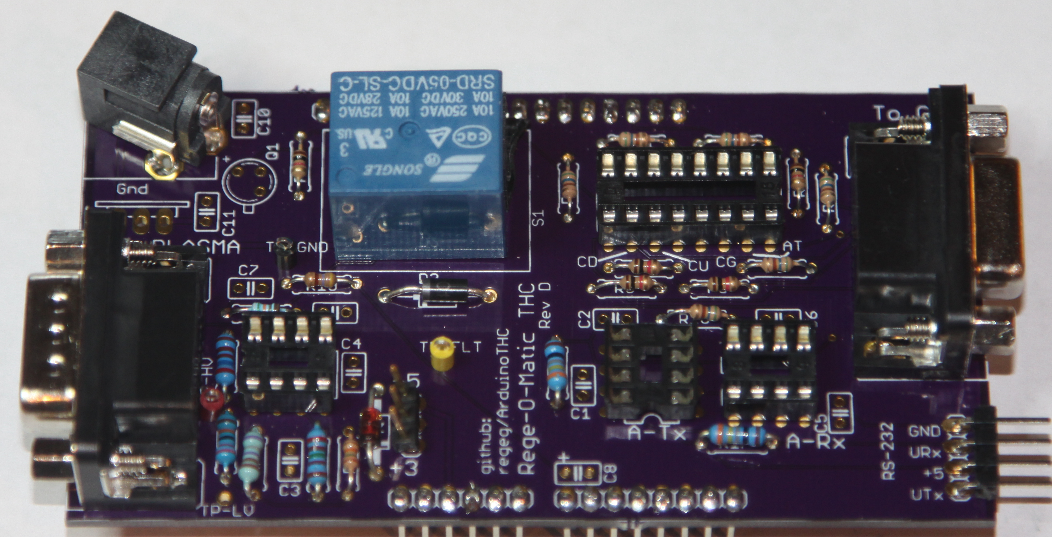
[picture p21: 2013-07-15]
THC Manual/THC Manual/BoardWithRelay.JPG

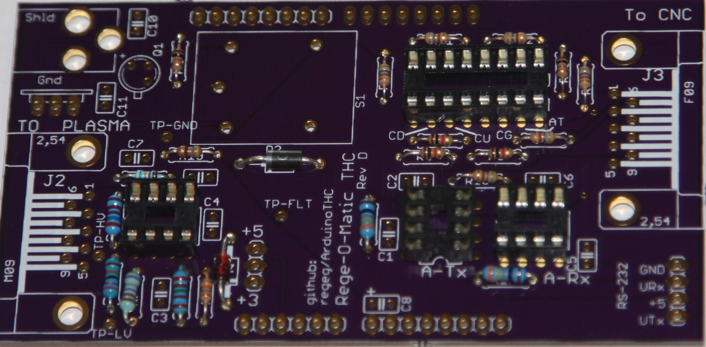
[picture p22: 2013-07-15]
THC Manual/THC Manual/BareBoard.JPG

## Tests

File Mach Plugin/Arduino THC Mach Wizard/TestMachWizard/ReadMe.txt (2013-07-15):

========================================================================
    CONSOLE APPLICATION : ArduinoTHC Project Overview
========================================================================

AppWizard has created this ArduinoTHC application for you.
========================================================================
    DYNAMIC LINK LIBRARY : ArduinoTHC Project Overview
========================================================================

AppWizard has created this ArduinoTHC DLL for you.
========================================================================
    STATIC LIBRARY : ArduinoTHC Project Overview
========================================================================

AppWizard has created this ArduinoTHC library project for you.
========================================================================
    WIN32 APPLICATION : ArduinoTHC Project Overview
========================================================================

AppWizard has created this ArduinoTHC application for you.

This file contains a summary of what you will find in each of the files that
make up your ArduinoTHC application.

ArduinoTHC.vcproj
    This is the main project file for VC++ projects generated using an Application Wizard.
    It contains information about the version of Visual C++ that generated the file, and
    information about the platforms, configurations, and project features selected with the
    Application Wizard.

/////////////////////////////////////////////////////////////////////////////
Other notes:

AppWizard uses "TODO:" comments to indicate parts of the source code you
should add to or customize.

/////////////////////////////////////////////////////////////////////////////

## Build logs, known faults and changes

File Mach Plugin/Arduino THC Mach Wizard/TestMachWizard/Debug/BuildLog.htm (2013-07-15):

Build Log

| | Build started: Project: ArduinoTHC, Configuration: Debug|Win32

Command Lines

Creating temporary file "c:\Users\Rege\Documents\Visual Studio 2008\Projects\TestMachWizard\TestMachWizard\Debug\RSP00000130762808.rsp" with contents
[
/Od /I "C:\Program Files (x86)\Joshua 1 Systems\MachPluginWizard\MachIncludes" /D "WIN32" /D "_DEBUG" /D "_WINDOWS" /D "_USRDLL" /D "_EXPORTS" /D "_WINDLL" /D "_MBCS" /FD /EHa /MDd /Yu"stdafx.h" /Fp"Debug\ArduinoTHC.pch" /Fo"Debug\\" /Fd"Debug\vc90.pdb" /W3 /c /Zi /clr /TP /FU "c:\Windows\Microsoft.NET\Framework\v2.0.50727\System.dll" /FU "c:\Windows\Microsoft.NET\Framework\v2.0.50727\System.Data.dll" /FU "c:\Windows\Microsoft.NET\Framework\v2.0.50727\System.Drawing.dll" /FU "c:\Windows\Microsoft.NET\Framework\v2.0.50727\System.Windows.Forms.dll" /FU "c:\Windows\Microsoft.NET\Framework\v2.0.50727\System.XML.dll"

".\ConfigDialog.cpp"
]
Creating command line "cl.exe @"c:\Users\Rege\Documents\Visual Studio 2008\Projects\TestMachWizard\TestMachWizard\Debug\RSP00000130762808.rsp" /nologo /errorReport:prompt"
Creating temporary file "c:\Users\Rege\Documents\Visual Studio 2008\Projects\TestMachWizard\TestMachWizard\Debug\RSP00000230762808.rsp" with contents
[
/OUT:"C:\Users\Rege\Documents\Visual Studio 2008\Projects\TestMachWizard\Debug\ArduinoTHC.dll" /INCREMENTAL /DLL /MANIFEST /MANIFESTFILE:"Debug\ArduinoTHC.dll.intermediate.manifest" /MANIFESTUAC:"level='asInvoker' uiAccess='false'" /DEBUG /ASSEMBLYDEBUG /PDB:"c:\Users\Rege\Documents\Visual Studio 2008\Projects\TestMachWizard\Debug\ArduinoTHC.pdb" /SUBSYSTEM:WINDOWS /DYNAMICBASE /FIXED:No /NXCOMPAT /MACHINE:X86 kernel32.lib user32.lib gdi32.lib winspool.lib comdlg32.lib advapi32.lib shell32.lib ole32.lib oleaut32.lib uuid.lib odbc32.lib odbccp32.lib /ASSEMBLYRESOURCE:".\Debug\TestMachWizard.ComError.resources" /ASSEMBLYRESOURCE:".\Debug\TestMachWizard.ConfigDialog.resources" /ASSEMBLYRESOURCE:".\Debug\TestMachWizard.PlugInControlDialog.resources" /ASSEMBLYRESOURCE:".\Debug\TestMachWizard.XYZDemoDialog.resources"

".\Debug\ConfigDialog.obj"

".\Debug\dllmain.obj"

".\Debug\MachDevice.obj"

".\Debug\Plugin.obj"

".\Debug\PlugInControlDialog.obj"

".\Debug\stdafx.obj"

".\Debug\THCSerialInterface.obj"

".\Debug\XYZDemoDialog.obj"

".\Debug\ComError.obj"
]
Creating command line "link.exe @"c:\Users\Rege\Documents\Visual Studio 2008\Projects\TestMachWizard\TestMachWizard\Debug\RSP00000230762808.rsp" /NOLOGO /ERRORREPORT:PROMPT"
Creating temporary file "c:\Users\Rege\Documents\Visual Studio 2008\Projects\TestMachWizard\TestMachWizard\Debug\RSP00000330762808.rsp" with contents
[
/outputresource:"..\Debug\ArduinoTHC.dll;#2" /manifest

".\Debug\ArduinoTHC.dll.intermediate.manifest"
]
Creating command line "mt.exe @"c:\Users\Rege\Documents\Visual Studio 2008\Projects\TestMachWizard\TestMachWizard\Debug\RSP00000330762808.rsp" /nologo"
Creating temporary file "c:\Users\Rege\Documents\Visual Studio 2008\Projects\TestMachWizard\TestMachWizard\Debug\BAT00000430762808.bat" with contents
[
@echo Manifest resource last updated at %TIME% on %DATE% > ".\Debug\mt.dep"
]
Creating command line """c:\Users\Rege\Documents\Visual Studio 2008\Projects\TestMachWizard\TestMachWizard\Debug\BAT00000430762808.bat"""
Creating temporary file "c:\Users\Rege\Documents\Visual Studio 2008\Projects\TestMachWizard\TestMachWizard\Debug\BAT00000530762808.bat" with contents
[
@echo off

copy "c:\Users\Rege\Documents\Visual Studio 2008\Projects\TestMachWizard\Debug\ArduinoTHC.dll" \Mach3\PlugIns

if errorlevel 1 goto VCReportError

goto VCEnd

:VCReportError

echo Project : error PRJ0019: A tool returned an error code from "Performing Post-Build Event..."

exit 1

:VCEnd
]
Creating command line """c:\Users\Rege\Documents\Visual Studio 2008\Projects\TestMachWizard\TestMachWizard\Debug\BAT00000530762808.bat"""

Output Window

| | Compiling... ConfigDialog.cpp Linking... Creating library C:\Users\Rege\Documents\Visual Studio 2008\Projects\TestMachWizard\Debug\ArduinoTHC.lib and object C:\Users\Rege\Documents\Visual Studio 2008\Projects\TestMachWizard\Debug\ArduinoTHC.exp Embedding manifest... Performing Post-Build Event... 1 file(s) copied.

Results

| | Build log was saved at "file://c:\Users\Rege\Documents\Visual Studio 2008\Projects\TestMachWizard\TestMachWizard\Debug\BuildLog.htm" ArduinoTHC - 0 error(s), 0 warning(s)

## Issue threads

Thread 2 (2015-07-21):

Status request

mariusl, 2015-07-21:
Hi
Not really an issue but rather asking what the status of the project is currently.
Do you use the project with your plasma and how is it performing?
I am looking at using it with a DC motor on the Z axis so I will have to make some changes to the code  and hardware to drive the motor but I will only start making changes if you feel it is stable as it is at this moment.

regeg, 2015-07-22:
I've had minimal feedback on the software.  I know that one or two people have it up and running.

But.... this was designed assuming that Mach would be doing the Z-height control.  I don't know if you'd have good enough latency to do the control with the Arduino.  I'd also recommend a touch and go head so that any problems during use don't do a hard physical crash of the plasma tip.  Again, the touch and go switch needs a very low latency response too.

mariusl, 2015-07-22:
I was wondering about the latency. It just means I have to replace the DC motor with a stepper on Z and let Mach do the work.
Thanks for the feedback.

Closed 2015-07-22.

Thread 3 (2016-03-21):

Marlin for plasma

mkeyno, 2016-03-21:
hi, have you tried or know someone to used the marlin to control the THC on plasma machine?
BR

regeg, 2016-03-22:
I'm not aware of anyone who has done that.  I'm not sure it would work because of the low amperage of the marlin boards.

Closed 2016-03-22.

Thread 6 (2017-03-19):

Cant't Compile the Mach3 Plugin

sallos, 2017-03-19:
I have very many error when I try to compile the plugin ...

What version of VS are you using? And with OS?

regeg, 2017-03-19:
I haven't done anything with that lately and don't have access to the PC that I built it on.
Check the document that I wrote and the Machine SDK.  I believe is was VS8.
One way to figure it out is to download the Machine SDK and get it to build the examples.
-------- Original message --------From: sallos <notifications@github.com> Date: 3/19/17  6:39 PM  (GMT-05:00) To: regeg/ArdunioTHC <ArdunioTHC@noreply.github.com> Cc: Subscribed <subscribed@noreply.github.com> Subject: [regeg/ArdunioTHC] Cant't Compile the Mach3 Plugin (#6)
I have very many error when I try to compile the plugin ...
What version of VS are you using? And with OS?

—
You are receiving this because you are subscribed to this thread.
Reply to this email directly, view it on GitHub, or mute the thread.

{"api_version":"1.0","publisher":{"api_key":"05dde50f1d1a384dd78767c55493e4bb","name":"GitHub"},"entity":{"external_key":"github/regeg/ArdunioTHC","title":"regeg/ArdunioTHC","subtitle":"GitHub repository","main_image_url":"https://cloud.githubusercontent.com/assets/143418/17495839/a5054eac-5d88-11e6-95fc-7290892c7bb5.png","avatar_image_url":"https://cloud.githubusercontent.com/assets/143418/15842166/7c72db34-2c0b-11e6-9aed-b52498112777.png","action":{"name":"Open in GitHub","url":"https://github.com/regeg/ArdunioTHC"}},"updates":{"snippets":[{"icon":"DESCRIPTION","message":"Cant't Compile the Mach3 Plugin (#6)"}],"action":{"name":"View Issue","url":"https://github.com/regeg/ArdunioTHC/issues/6"}}}

sallos, 2017-03-19:
Mh okay would have used your plugin as a basis.

I want to build a thc for my hyptherm, get a 50: 1 voltage output

sallos, 2017-03-20:
Iam using vb2008 an this Error i have:

Warning	1	Command line warning D9035 : option 'Wp64' has been deprecated and will be removed in a future release	cl	ArduinoTHC
Error	2	error C2504: 'CObject' : base class undefined	c:\users\ls\seafile\daten\projekte\plasma cnc\thc work\mach3\machincludes\memmap.h	34	ArduinoTHC
Error	3	error C4430: missing type specifier - int assumed. Note: C++ does not support default-int	c:\users\ls\seafile\daten\projekte\plasma cnc\thc work\mach3\machincludes\memmap.h	41	ArduinoTHC
Error	4	error C2143: syntax error : missing ',' before '&'	c:\users\ls\seafile\daten\projekte\plasma cnc\thc work\mach3\machincludes\memmap.h	41	ArduinoTHC
Error	5	error C4430: missing type specifier - int assumed. Note: C++ does not support default-int	c:\users\ls\seafile\daten\projekte\plasma cnc\thc work\mach3\machincludes\memmap.h	45	ArduinoTHC
Error	6	error C2143: syntax error : missing ',' before '&'	c:\users\ls\seafile\daten\projekte\plasma cnc\thc work\mach3\machincludes\memmap.h	45	ArduinoTHC
Error	7	error C4430: missing type specifier - int assumed. Note: C++ does not support default-int	c:\users\ls\seafile\daten\projekte\plasma cnc\thc work\mach3\machincludes\memmap.h	47	ArduinoTHC
Error	8	error C2143: syntax error : missing ',' before '&'	c:\users\ls\seafile\daten\projekte\plasma cnc\thc work\mach3\machincludes\memmap.h	47	ArduinoTHC
Error	9	error C2146: syntax error : missing ';' before identifier 'GetMappingName'	c:\users\ls\seafile\daten\projekte\plasma cnc\thc work\mach3\machincludes\memmap.h	54	ArduinoTHC
Error	10	error C4430: missing type specifier - int assumed. Note: C++ does not support default-int	c:\users\ls\seafile\daten\projekte\plasma cnc\thc work\mach3\machincludes\memmap.h	54	ArduinoTHC
Error	11	error C4430: missing type specifier - int assumed. Note: C++ does not support default-int	c:\users\ls\seafile\daten\projekte\plasma cnc\thc work\mach3\machincludes\memmap.h	54	ArduinoTHC
Warning	12	warning C4183: 'GetMappingName': missing return type; assumed to be a member function returning 'int'	c:\users\ls\seafile\daten\projekte\plasma cnc\thc work\mach3\machincludes\memmap.h	54	ArduinoTHC
Error	13	error C3646: 'BOOL' : unknown override specifier	c:\users\ls\seafile\daten\projekte\plasma cnc\thc work\mach3\machincludes\memmap.h	70	ArduinoTHC
Error	14	error C3646: 'MapHandle' : unknown override specifier	c:\users\ls\seafile\daten\projekte\plasma cnc\thc work\mach3\machincludes\memmap.h	70	ArduinoTHC
Error	15	error C2091: function returns function	c:\users\ls\seafile\daten\projekte\plasma cnc\thc work\mach3\machincludes\memmap.h	70	ArduinoTHC
Error	16	error C4430: missing type specifier - int assumed. Note: C++ does not support default-int	c:\users\ls\seafile\daten\projekte\plasma cnc\thc work\mach3\machincludes\memmap.h	70	ArduinoTHC
Warning	17	warning C4183: 'DECLARE_DYNAMIC': missing return type; assumed to be a member function returning 'int'	c:\users\ls\seafile\daten\projekte\plasma cnc\thc work\mach3\machincludes\memmap.h	70	ArduinoTHC
Error	18	error C2146: syntax error : missing ';' before identifier 'CreateMappingName'	c:\users\ls\seafile\daten\projekte\plasma cnc\thc work\mach3\machincludes\memmap.h	71	ArduinoTHC
Error	19	error C4430: missing type specifier - int assumed. Note: C++ does not support default-int	c:\users\ls\seafile\daten\projekte\plasma cnc\thc work\mach3\machincludes\memmap.h	71	ArduinoTHC
Error	20	error C4430: missing type specifier - int assumed. Note: C++ does not support default-int	c:\users\ls\seafile\daten\projekte\plasma cnc\thc work\mach3\machincludes\memmap.h	71	ArduinoTHC
Error	21	error C2143: syntax error : missing ',' before '&'	c:\users\ls\seafile\daten\projekte\plasma cnc\thc work\mach3\machincludes\memmap.h	71	ArduinoTHC
Error	22	error C4430: missing type specifier - int assumed. Note: C++ does not support default-int	c:\users\ls\seafile\daten\projekte\plasma cnc\thc work\mach3\machincludes\memmap.h	71	ArduinoTHC
Warning	23	warning C4183: 'CreateMappingName': missing return type; assumed to be a member function returning 'int'	c:\users\ls\seafile\daten\projekte\plasma cnc\thc work\mach3\machincludes\memmap.h	71	ArduinoTHC
Error	24	error C2146: syntax error : missing ';' before identifier 'CreateMutexName'	c:\users\ls\seafile\daten\projekte\plasma cnc\thc work\mach3\machincludes\memmap.h	72	ArduinoTHC
Error	25	error C4430: missing type specifier - int assumed. Note: C++ does not support default-int	c:\users\ls\seafile\daten\projekte\plasma cnc\thc work\mach3\machincludes\memmap.h	72	ArduinoTHC
Error	26	error C4430: missing type specifier - int assumed. Note: C++ does not support default-int	c:\users\ls\seafile\daten\projekte\plasma cnc\thc work\mach3\machincludes\memmap.h	72	ArduinoTHC
Warning	27	warning C4183: 'CreateMutexName': missing return type; assumed to be a member function returning 'int'	c:\users\ls\seafile\daten\projekte\plasma cnc\thc work\mach3\machincludes\memmap.h	72	ArduinoTHC
Error	28	error C2146: syntax error : missing ';' before identifier 'm_sMappingName'	c:\users\ls\seafile\daten\projekte\plasma cnc\thc work\mach3\machincludes\memmap.h	79	ArduinoTHC
Error	29	error C4430: missing type specifier - int assumed. Note: C++ does not support default-int	c:\users\ls\seafile\daten\projekte\plasma cnc\thc work\mach3\machincludes\memmap.h	79	ArduinoTHC
Error	30	error C4430: missing type specifier - int assumed. Note: C++ does not support default-int	c:\users\ls\seafile\daten\projekte\plasma cnc\thc work\mach3\machincludes\memmap.h	79	ArduinoTHC
Error	31	error C2065: 'm_sMappingName' : undeclared identifier	c:\users\ls\seafile\daten\projekte\plasma cnc\thc work\mach3\machincludes\memmap.h	54	ArduinoTHC
Error	32	error C2146: syntax error : missing ';' before identifier 'description'	c:\users\ls\seafile\daten\projekte\plasma cnc\thc work\mach3\machincludes\toolcabinet.h	9	ArduinoTHC
Error	33	error C4430: missing type specifier - int assumed. Note: C++ does not support default-int	c:\users\ls\seafile\daten\projekte\plasma cnc\thc work\mach3\machincludes\toolcabinet.h	9	ArduinoTHC

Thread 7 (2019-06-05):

Unable to understand how to upload sketch on arduino

mpstmpart, 2019-06-05:
Hi,
I just downloaded the zip file but under arduino source folder i found 22 files of C/C++ and some other file, i just wanted to know that wich file i can use as arduino sketch or i need to convert that all file into hex or something else Beacause i am new with arduino.
 Please help me because i have have build the PCB and all hardwares.

saxa, 2019-06-05:
Hi I also follow this project, I will probably try to make one of those for me too. But I am still far away of having the need for making it. It should work most probably if you interface everything correctly.

vatsal1452, 2020-07-23:
Yes it might work as relay is used for such purposes

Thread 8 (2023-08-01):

Mach3 Plugin, Unable to connect to port.

Anthony-Andrews, 2023-08-01:
I'm aware this project is quite old at this point but if anyone had any help or suggestions that would be hugely appreciated.

**Setup to recreate:**
Rev E. Micro board, tested working with the standalone application.
Mach3 Version R3.043.066 on Windows 10 with the latest .dll ArduinoTHC plugin and "plasmaTHC.set" file renamed to "plasma.set".
The GUI is working and displays the custom tab. In the config plugins tab it displays "ArduinoTHC-RegeG-v0.0.0.0"

**Problem:**
_In the Arduino THC Configuration tab it lists the port (COM4) of the THC but is does not save the selected port. It is instead stuck saying "Current Port: COM1" even after a Mach3 Restart._

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

**Debugging steps:**
I have tried the latest version of Mach3 where the plugin is marked as defective, and have tried older versions of the plugin which also are marked as defective. I have also tried running as admin, and in compatability mode as Windows XP all to no avail.

Next up would be to find an older version of Mach3 and possibly use native Windows XP.

Anthony-Andrews, 2023-08-02:
Solved. My version of Mach3 must have been corrupted as even though I had tried the latest version of Mach before, I tried again after a clean install and it worked flawlessly with the plugin.

Closed 2023-08-02.

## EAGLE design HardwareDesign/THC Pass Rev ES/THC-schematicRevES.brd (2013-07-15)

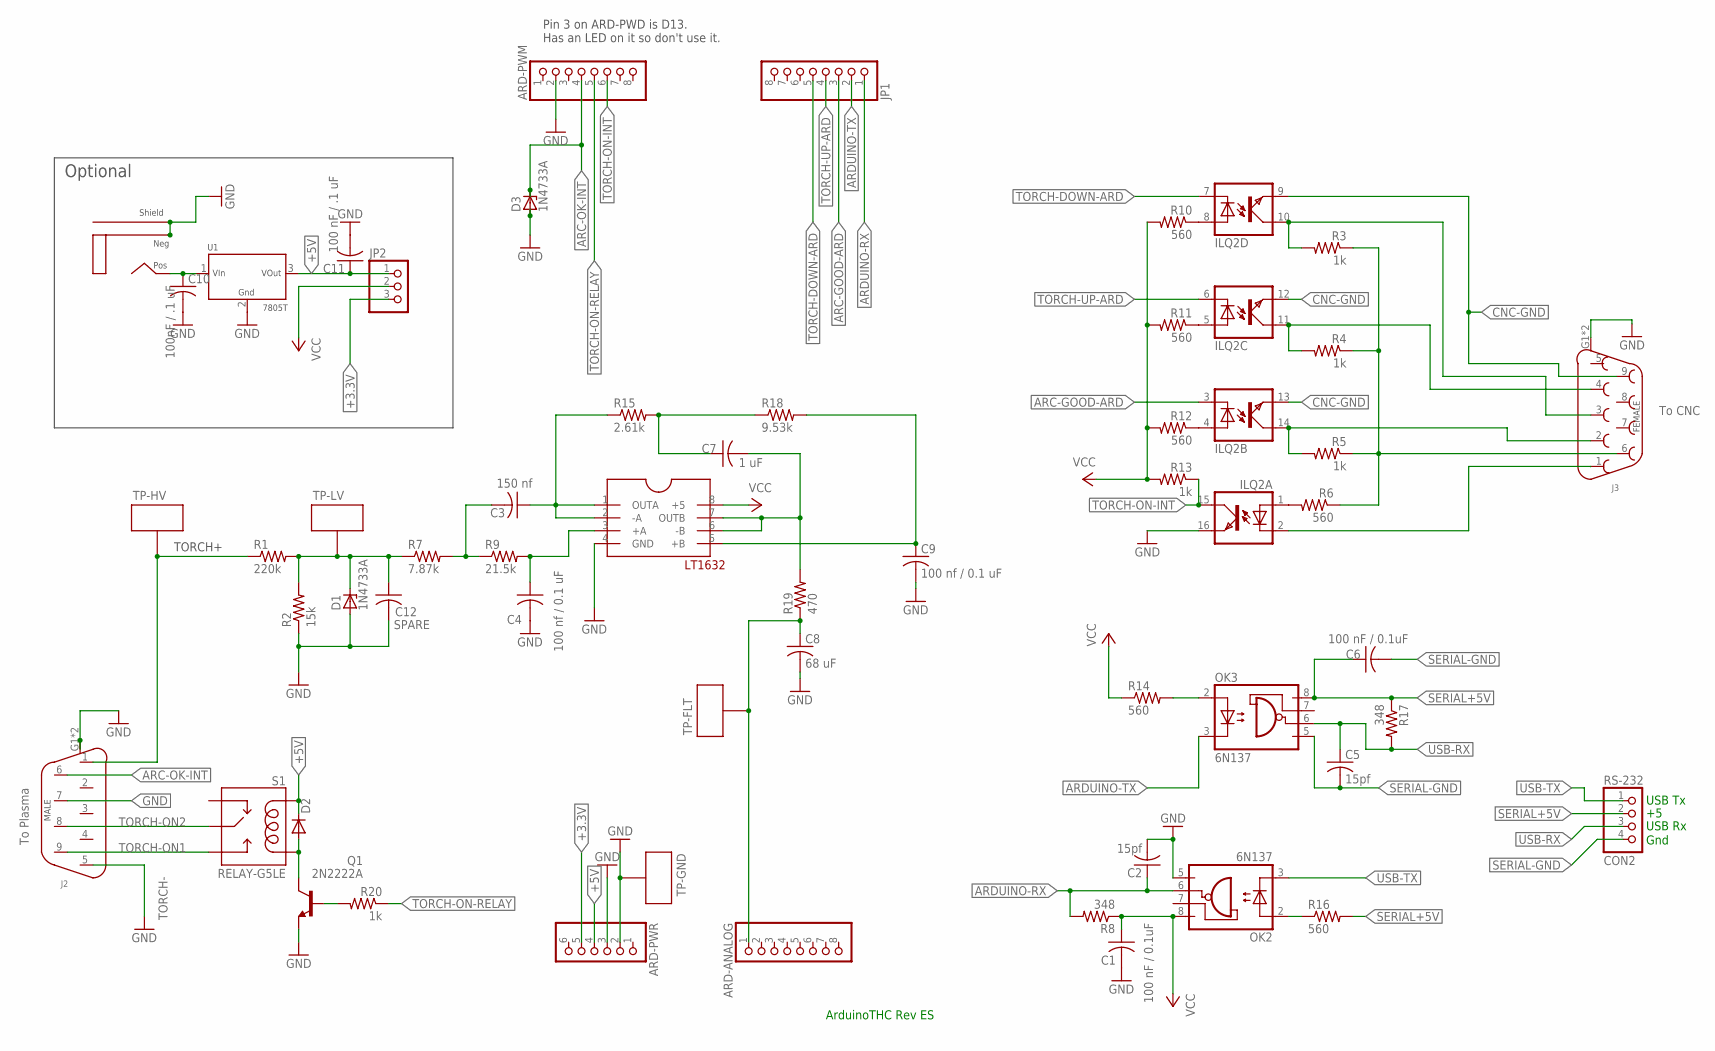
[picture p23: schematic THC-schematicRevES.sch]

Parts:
ARD-ANALOG: PINHD-1X8; 1X08
ARD-PWM: PINHD-1X8; 1X08
ARD-PWR: PINHD-1X6; 1X06
C1, C6: 100 nF / 0.1uF; C025-025X050
C2, C5: 15pf; C025-025X050
C3: 150 nf; C025-025X050
C4, C9: 100 nf / 0.1 uF; C025-025X050
C7: 1 uF; C025-025X050
C8: 68 uF; C025-025X050
C10: 100nF / .1 uF; C025-025X050
C11: 100 nF / .1 uF; C025-025X050
C12: SPARE; C025-025X050
D1, D3: 1N4733A; DO41Z10
D2: 1N4001; DO-204AL
ILQ2: ILQ1; DIL16
J1: 2.1MM-PLUG-PCB-MNT; 2.1MM-PLUG
J2: DB9-MALE; DB9M-RIGHT-ANGLE
J3: DB9-FEMALE; DB9F-RIGHT-ANGLE
JP1: PINHD-1X8; 1X08
JP2: PINHD-1X3; 1X03
OK2, OK3: 6N137; DIL08
Q1: 2N2222A; TO18
R1: 220k; 0207/7
R2: 15k; 0207/7
R3, R4, R5, R13, R20: 1k; 0207/7
R6, R10, R11, R12, R14, R16: 560; 0207/7
R7: 7.87k; 0207/7
R8, R17: 348; 0207/7
R9: 21.5k; 0207/7
R15: 2.61k; 0207/7
R18: 9.53k; 0207/7
R19: 470; 0207/7
RS-232: CON2; 1X04
S1: RELAY-G5LE
TP-FLT: TEST-POINT-.040-HOLE; TP.040
TP-GND: TEST-POINT-.040-HOLE; TP.040
TP-HV: TEST-POINT-.040-HOLE; TP.040
TP-LV: TEST-POINT-.040-HOLE; TP.040
U1: 7805T; TO-220-3
U$1: LT1632; DIP08

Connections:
+3.3V: ARD-PWR.5, JP2.3
+5V: ARD-PWR.4, C11.1, D2.C, JP2.1, S1.P$5-COIL (COIL-2), U1.3 (VOUT)
ARC-GOOD-ARD: ILQ2.3 (C), JP1.3
ARC-OK-INT: ARD-PWM.4, D3.C, J2.6
ARD-ANALOG-IN: ARD-ANALOG.1, C8.1, R19.1, TP-FLT.P$1
ARDUINO-RX: C2.1, JP1.1, OK2.6 (VO), R8.2
ARDUINO-TX: JP1.2, OK3.3 (C)
CNC+5: J3.6, R3.1, R4.1, R5.1, R6.1
CNC-ARC-GOOD: ILQ2.14 (COL), J3.2, R5.2
CNC-GND: ILQ2.9 (EMIT), ILQ2.12 (EMIT), ILQ2.13 (EMIT), J3.9
CNC-TORCH-DOWN: ILQ2.10 (COL), J3.3, R3.2
CNC-TORCH-ON: ILQ2.2 (C), J3.1
CNC-TORCH-UP: ILQ2.11 (COL), J3.4, R4.2
DIVIDER: C12.1, D1.C, R1.2, R2.2, R7.1, TP-LV.P$1
GND: ARD-PWM.2, ARD-PWR.2, ARD-PWR.3, C1.2, C2.2, C4.2, C8.2, C9.2, C10.2, C11.2, C12.2, D1.A, D3.A, ILQ2.16 (EMIT), J1.P$NEG, J1.P$SHLD, J2.5, J2.7, J2.G1 (P$SHLD), J2.G2 (P$SHLD), J3.G1 (P$SHLD), J3.G2 (P$SHLD), OK2.5 (GND), Q1.1 (E), R2.1, TP-GND.P$1, U1.2 (GND), U$1.4 (GND)
unnamed: C10.1, J1.P$POS, U1.1 (VIN)
unnamed: ILQ2.4 (A), R12.1
unnamed: D2.A, Q1.3 (C), S1.P$2-COIL (COIL-1)
unnamed: Q1.2 (B), R20.2
unnamed: ILQ2.5 (A), R11.1
unnamed: ILQ2.8 (A), R10.1
unnamed: ILQ2.1 (A), R6.2
unnamed: C3.2, R7.2, R9.1
unnamed: C4.1, R9.2, U$1.3 (+A)
unnamed: C3.1, R15.1, U$1.1 (OUTA), U$1.2 (-A)
unnamed: C7.1, R15.2, R18.1
unnamed: C9.1, R18.2, U$1.5 (+B)
unnamed: OK3.2 (A), R14.2
unnamed: OK2.2 (A), R16.1
SERIAL+5V: C6.1, OK3.8 (VCC), R16.2, R17.1, RS-232.2
SERIAL-GND: C5.2, C6.2, OK3.5 (GND), RS-232.4
TORCH+: J2.1, R1.1, TP-HV.P$1
TORCH-DOWN-ARD: ILQ2.7 (C), JP1.5
TORCH-ON1: J2.9, S1.P$4-NO (NO)
TORCH-ON2: J2.8, S1.P$1-COMMON (COM)
TORCH-ON-INT: ARD-PWM.6, ILQ2.15 (COL), R13.1
TORCH-ON-RELAY: ARD-PWM.5, R20.1
TORCH-UP-ARD: ILQ2.6 (C), JP1.4
UNFILTERED: C7.2, R19.2, U$1.6 (-B), U$1.7 (OUTB)
USB-RX: C5.1, OK3.6 (VO), R17.2, RS-232.3
USB-TX: OK2.3 (C), RS-232.1
VCC: C1.1, JP2.2, OK2.8 (VCC), R8.1, R10.2, R11.2, R12.2, R13.2, R14.1, U$1.8 (+5)

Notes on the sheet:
USB Tx
USB Rx
Gnd
ArduinoTHC Rev ES
To Plasma
To CNC
TORCH-
Pin 3 on ARD-PWD is D13. Has an LED on it so don't use it.
TORCH+
Optional

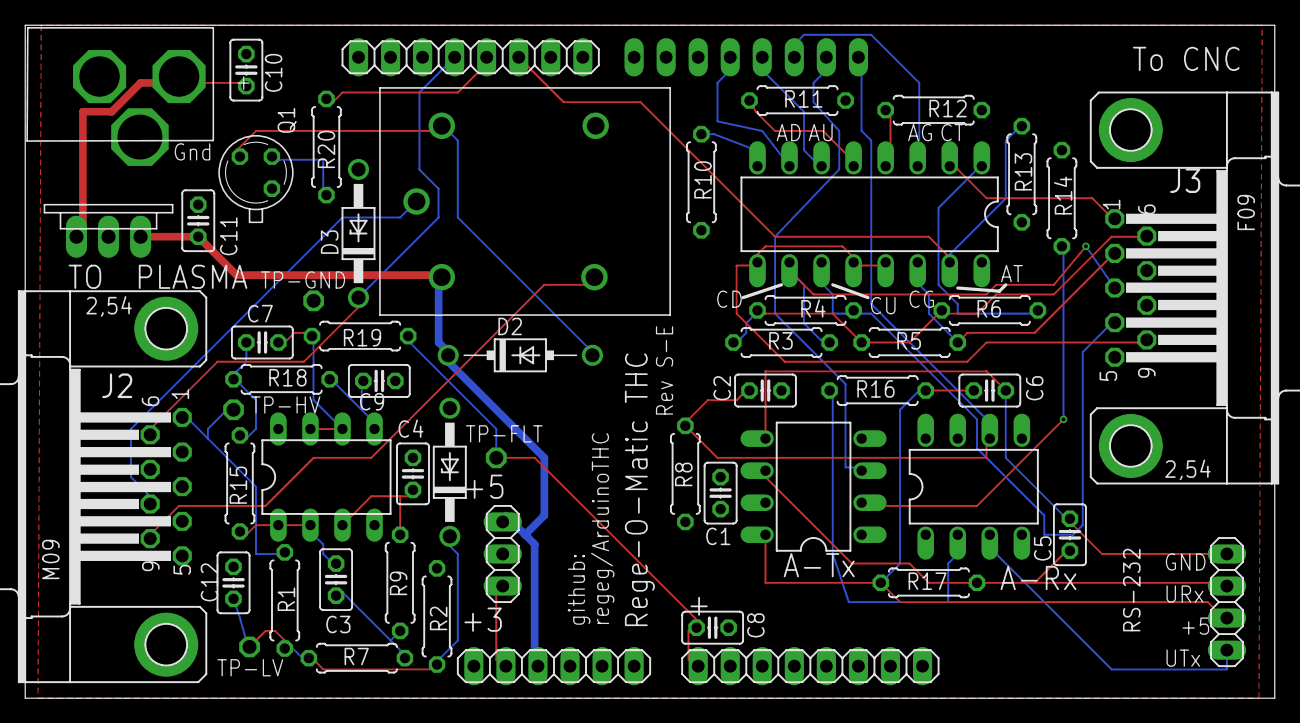
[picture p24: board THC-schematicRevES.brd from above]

Board: 2 copper layers, 99.0 x 53.3 mm, 55 parts (1 on the bottom side), 42 nets.

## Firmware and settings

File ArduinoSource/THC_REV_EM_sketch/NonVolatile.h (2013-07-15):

/*
* COPYRIGHT 2013 - Regis M. George
 *
 * License: Creative Commons Attribution-NonCommercial-ShareAlike 3.0 Unported License
 *
*/

/*
 * NonVolatile.hpp
 *
 * The NonVolatile class will maintain the THC settings and usage
 * data in the EEPROM on the Arduino.  It uses a checksum byte
 * to determine if the memory is blank or corrupt.  If blank
 * or corrupt, it will re-initialize the flahs.
 * Since the EEPROM has a limited number of writes, the write
 * count is tracked and if the write limit is exceeded, then
 * the block of memory used is moved up in EEPROM.
 *
 *  Created on: Sep 22, 2012
 *      Author: Rege
 */
#ifndef NONVOLATILE_HPP_
#define NONVOLATILE_HPP_

#include "THC.h"

// Define the memory map of data saved in EEPROM.
#define ADDR_OFFSET			0  // The offset is the offset to the memory block holding the data.
					   // This is ALWAYS at the absolute 0 address in the flash.

// The following bytes are relative offsets within the block of memory
#define REL_ADDR_CHECK_BYTE 		 0
#define REL_ADDR_VOLT_SETPOINT_B1 	1
#define REL_ADDR_VOLT_SETPOINT_B2 	2
#define REL_ADDR_VOLT_SCALING		3
#define REL_ADDR_PILOT_ARC_COUNT_BYTE1 	4
#define REL_ADDR_PILOT_ARC_COUNT_BYTE2 	5
#define REL_ADDR_PIERCE_COUNT_BYTE1    	6
#define REL_ADDR_PIERCE_COUNT_BYTE2    	7
#define REL_ADDR_TIP_HOURS_BYTE			8
#define REL_ADDR_TIP_MINUTES_BYTE		9
#define REL_ADDR_TIP_SECONDS_BYTE		10
#define REL_ADDR_WRITE_COUNT_BYTE1		11
#define REL_ADDR_WRITE_COUNT_BYTE2		12
#define REL_ADDR_WRITE_COUNT_BYTE3		13
#define REL_ADDR_WRITE_COUNT_BYTE4		14
#define REL_ADDR_DEFAULT_STATE			15

#define MEMORY_BLOCK_SIZE				16

// Define default values for a new system.
#define DEFAULT_SCALE 		40
#define DEFAULT_SET_POINT 	600


// The magic number is used to see if the EEPROM has
// been initialized.
#define EEPROM_MAGIC_NUMBER 42


// Set the max number of writes before using
// the next sequential block of EEPROM
#define WRITE_LIMIT 95000L



//
// This class handles all persistent data kept in EEPROM.
//
class NonVolatileStorage {

private:
	bool initialized;
	unsigned char addrOffset;
	unsigned char scale;
	unsigned int  pilotArcCount;
	unsigned int  pierceCount;
	unsigned char tipHours;
	unsigned char tipMinutes;
	unsigned char tipSeconds;
	unsigned int voltSetPoint;
	unsigned long writeCount;
	THCState_e defaultState;

	void InitializeStorage(unsigned char addrOffsetParam);

public:
	NonVolatileStorage();

	void DataLoad(void);
	void DataSave(void);
	void DataReset(void);

	void DataGetAll(THCStatData *data);
	void DataSetAll(THCStatData *data);

	unsigned char ScalingGet(void);
	void ScalingSet(unsigned char);

	unsigned int PilotArcCountGet(void);
	void PilotArcCountSet(unsigned int);

	unsigned int PierceCountGet(void);
	void PierceCountSet(unsigned int);

	unsigned char TipHoursGet(void);
	void TipHoursSet(unsigned char);

	unsigned char TipMinutesGet(void);
	void TipMinutesSet(unsigned char);

	unsigned char WriteCountGet(void);

	unsigned int VoltSetPointGet(void);
	void VoltSetPointSet(unsigned int);

	THCState_e DefaultStateGet(void);
	void DefaultStateSet(THCState_e state);

	unsigned char getBlock(void);
	unsigned char setBlock(unsigned char newBlock);

};


#endif /* NONVOLATILE_HPP_ */

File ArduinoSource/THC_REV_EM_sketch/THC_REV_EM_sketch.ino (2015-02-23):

/*
 * COPYRIGHT 2013 - Regis M. George
 *
 * License: Creative Commons Attribution-NonCommercial-ShareAlike 3.0 Unported License
 *
 */
#include <EEPROM.h>
#include "Arduino.h"

#include "THC.h"

#include "Platform.h"

#include "HardwareSerial.h"

#include "IOConfig.h"
#include "Timer.h"
#include "IO.h"
#include "NonVolatile.h"

#include "StateEnabled.h"
#include "StateCutting.h"
#include "BypassMode.h"
#include "IO.h"
#include "Messages.h"

//
// Global Declarations
//
// Given the size and complexity of this application, its reasonable
// to just make the key variables global.
//

// Object used to maintain configuration information in flash.
NonVolatileStorage flash;

// Key global data structure.
StateData currentStateData;

// Tip usage parameters.
volatile THCStatData usageData;

// Flag value to determine when to send cutting voltages.
bool captureOn = true;

unsigned int displayUpdateDelay = 0;




//
// AddSecondsToTipUse()
//
// The amount of time cutting is maintained in the "usageData"
// structure so consumables life can be tracked.  When adding
// cutting time you add seconds, but it can effect minutes
// and hours.  So do the math properly.
//
void AddSecondsToTipUse(THCStatData *usageData, unsigned int seconds)
{
	unsigned int temp;

	temp = (unsigned int) usageData->tipSeconds + seconds;
	usageData->tipSeconds = temp % 60;
	// Calculate the number of minutes rolled over
	temp = (temp / 60) + ((unsigned int) usageData->tipMinutes);
	usageData->tipMinutes = temp % 60;
	usageData->tipHours += (temp / 60);
}




//
// setup()
//
// Initialization routine that will get the THC up and running.
// It starts the serial port, does the call to setup all the
// inputs and outputs and loads saved settings from flash.
//
void setup()
{

	// Start the first serial port for development diag output
	SERIAL.begin(115200);

	// Initialize the state variables.
	currentStateData.torchOnState = false;
	currentStateData.arcGoodState = false;

	// Configure the I/O as the very first thing so
	// nothing gets turned on unexpectedly.
	setupIO();

	// Load all the data from the flash and set the default state.
	flash.DataLoad();
	flash.DataGetAll((THCStatData*) &usageData);
	//currentStateData.currentState = usageData.defaultState;
	currentStateData.currentMode = THC_MODE_OPERATING;
	currentStateData.currentState = THC_STATE_ENABLED;
	currentStateData.voltSetPoint = usageData.voltSetPoint;
	currentStateData.kerfEncountered = false;
	currentStateData.currentUnit = THC_UNIT_COUNTS;
// TEMP SET VOLTAGE
	currentStateData.voltSetPoint = 760;
}




//
// handleModeChange()
//
// This routine will cause the controller to step through the
// different operating modes sequentially, as long as the
// TorchOn or ArcGood are not active.
//
// The sequence that modes are stepped through is:
// - Disabled (doesn't pass through torch on/off commands)
// - Bypass (passes through commands so you can cut w/o THC control)
// - Cruise (passes through until you tell it to use the current voltage
//           as the set point and start THC control)
// - Enabled (normal THC control)
//
void handleModeChange()
{

	// Only allow mode change if there is no torch on or arc good signal
	// (this is a short-cut for checking to see if we're cutting.
	if (!currentStateData.torchOnState && !currentStateData.arcGoodState)
	{
		if (currentStateData.currentMode == THC_MODE_DISABLED)
		{
			currentStateData.currentMode = THC_MODE_BYPASS;
		}
		else if (currentStateData.currentMode == THC_MODE_BYPASS)
		{
			currentStateData.currentMode = THC_MODE_CRUISE;
		}
		else if (currentStateData.currentMode == THC_MODE_CRUISE)
		{
  			currentStateData.currentMode = THC_MODE_OPERATING;
			currentStateData.currentState = THC_STATE_ENABLED;
		}
		else if (currentStateData.currentMode == THC_MODE_OPERATING)
		{
			currentStateData.currentMode = THC_MODE_DISABLED;
		}
	}
}




// The loop function is called in an endless loop
void loop()
{
	bool oldTorchState = true;
	BypassMode *bypassHandler;
	unsigned long loopWaitTimer;
	unsigned int newVoltage;

	bypassHandler = new BypassMode();

	// Initialize the wait timer for the main loop.
	// This timer is used to ensure that you don't execute the control
	// loop any more often than every millisecond.
	loopWaitTimer = millis();

        oldTorchState = currentStateData.torchOnState = false;

	//
	// Main control loop for THC.
	//
	while (1)
	{
		// Ensure a millisecond has elapsed before running again.
		// This should give a little more consistent behavior.
		while (loopWaitTimer == millis())
		{
		}

		// Reset the timer for the next loop.
		loopWaitTimer = millis();

		//
		// READ THE TORCH VOLTAGE FROM THE PLASMA
		//
		newVoltage = analogRead(IN_A_VOLTAGE);
		// Filter any noise when off to 0.
		if (newVoltage <= ANALOG_VOLTAGE_NOISE_FLOOR)
			currentStateData.currentVoltage = 0;
		else
			currentStateData.currentVoltage = newVoltage;

		//
		// READ TORCH ON INPUT SIGNAL FROM CNC
		//
		currentStateData.torchOnState = (
				digitalRead(IN_D_TORCH_ON_PIN) == IN_D_TORCH_ON_PIN_ACTIVE ? true : false);

		// If the torch on state has changed, handle it.
		if (currentStateData.torchOnState != oldTorchState)
		{
			// Update saved torch on state.
			oldTorchState = currentStateData.torchOnState;

			// If the torch is being turned off, do it immediately.
			if (!currentStateData.torchOnState)
			{
				digitalWrite(OUT_D_TORCH_RELAY, OUT_D_TORCH_RELAY_NOT_ACTIVE);
			}
			// else If torch was turned on, let state machine logic decide
			// how to handle it.
		}

		//
		// READ THE ARC-GOOD STATE FROM THE PLASMA
		//
		ProcessArcGoodSignal();
        	if (currentStateData.arcStateChanged == true)
                  sendFullVoltageMessage();

		//
		// CHECK FOR COMMANDS FROM PC
		//
		// If there are serial characters present figure
		// out if there is a complete command packet, and
		// if so, process it.
		if (SERIAL.available() > 0)
		{
			uint8_t buff[10];
			uint16_t temp;

			// Look at the command (without "reading" it)
			switch (SERIAL.peek())
			{
			case PC_CMD_SYNC:
				// Read and throw away the sync byte.
				SERIAL.read();
				break;

			case PC_CMD_STEP_MODE:
				// Read and throw away the sync byte.
				SERIAL.read();
				handleModeChange();
				// Build and send the response.
				SendMode();
				break;

			case PC_CMD_GET_MODE:
				// Read the command byte and throw away.
				SERIAL.read();
				// Build and send the response.
				SendMode();
				break;

			case PC_CMD_STEP_UNIT:
				// Read the command byte and throw away.
				SERIAL.read();
				// Update the unit.
				// Change the units between volts and counts.
				if (currentStateData.currentUnit == THC_UNIT_COUNTS)
					currentStateData.currentUnit = THC_UNIT_VOLTS;
				else
					currentStateData.currentUnit = THC_UNIT_COUNTS;

				// Build and send the responses.
				SendUnits();
				SendVoltage(PC_RESP_SETPOINT);
				SendVoltage(PC_RESP_CURRENT);
				break;

			case PC_CMD_GET_UNIT:
				// Read the command byte and throw away.
				SERIAL.read();
				SendUnits();
				break;

			case PC_CMD_DISPLAY_ON_OFF:
				if (SERIAL.available() < 2)
					break;
				// Respond to the command.
				break;

			case PC_CMD_GET_STATUS:
				break;

			case PC_CMD_SET_SETPOINT:
				if (SERIAL.available() < 3)
					break;
				// Read the command byte and throw away.
				SERIAL.read();
				// Respond to the command.
				buff[0] = (uint8_t) SERIAL.read();
				buff[1] = (uint8_t) SERIAL.read();
				temp = (((uint16_t) buff[0]) << 8) | ((uint16_t) buff[1]);
				if (currentStateData.currentUnit == THC_UNIT_VOLTS)
					temp *= COUNTS_PER_VOLT;
				currentStateData.voltSetPoint = temp;
				SendVoltage(PC_RESP_SETPOINT);
				break;

			case PC_CMD_GET_SETPOINT:
				// Read the command byte and throw away.
				SERIAL.read();
				// Build and send the response.
				SendVoltage(PC_RESP_SETPOINT);
				break;

			case PC_CMD_GET_CURRENT:
				// Read the command byte and throw away.
				SERIAL.read();
				// Build and send the response.
				SendVoltage(PC_RESP_CURRENT);
				break;

			case PC_CMD_TEST_TORCH_ON:
				// Read the command byte and throw away.
				SERIAL.read();
				// Toggle the torch.
				TestTorchOn(true);
				break;

			case PC_CMD_TEST_TORCH_OFF:
				// Read the command byte and throw away.
				SERIAL.read();
				// Toggle the torch.
				TestTorchOn(false);
				break;

			case PC_CMD_CAPTURE_START:
				// Read the command byte and throw away.
				SERIAL.read();
				captureOn = true;
				sendVoltageCaptureState(captureOn);
				break;

			case PC_CMD_CAPTURE_STOP:
				// Read the command byte and throw away.
				SERIAL.read();
				captureOn = false;
				sendVoltageCaptureState(captureOn);
				break;

			case PC_CMD_CAPTURE_GET_STATE:
				// Read the command byte and throw away.
				SERIAL.read();
				sendVoltageCaptureState(captureOn);
				break;

			case PC_CMD_SETPOINT_UP:
				// Read the command byte and throw away.
				SERIAL.read();
				// Handle the up.
				if ((currentStateData.currentUnit == THC_UNIT_VOLTS)
						&& (currentStateData.voltSetPoint / COUNTS_PER_VOLT < 180))
				{
					currentStateData.voltSetPoint += COUNTS_PER_VOLT;
				}
				else if ((currentStateData.currentUnit == THC_UNIT_COUNTS)
						&& (currentStateData.voltSetPoint < 1020))
				{
					currentStateData.voltSetPoint++;
				}
				// Build and send the response.
				SendVoltage(PC_RESP_SETPOINT);
				// Update the LCD
				break;

			case PC_CMD_SETPOINT_DOWN:
				// Read the command byte and throw away.
				SERIAL.read();
				// Handle the down.
				if ((currentStateData.currentUnit == THC_UNIT_VOLTS)
						&& (currentStateData.voltSetPoint / COUNTS_PER_VOLT > 50))
				{
					currentStateData.voltSetPoint -= COUNTS_PER_VOLT;
				}
				else if ((currentStateData.currentUnit == THC_UNIT_COUNTS)
						&& (currentStateData.voltSetPoint > 350))
				{
					currentStateData.voltSetPoint--;
				}
				// Build and send the response.
				SendVoltage(PC_RESP_SETPOINT);
				// Update the LCD
				break;

			case PC_CMD_TEST_ARC_GOOD_ON:
				// Read the command byte and throw away.
				SERIAL.read();
				// Turn on arc good for test
				digitalWrite(OUT_D_ARC_GOOD, OUT_D_ARC_GOOD_ACTIVE);
				break;

			case PC_CMD_TEST_ARC_GOOD_OFF:
				// Read the command byte and throw away.
				SERIAL.read();
				// Turn off arc good for test
				digitalWrite(OUT_D_ARC_GOOD, OUT_D_ARC_GOOD_NOT_ACTIVE);
				break;

			case PC_CMD_TEST_THC_UP_ON:
				// Read the command byte and throw away.
				SERIAL.read();
				// Turn on torch up for test
				digitalWrite(OUT_D_TORCH_UP, OUT_D_TORCH_UP_ACTIVE);
				break;

			case PC_CMD_TEST_THC_UP_OFF:
				// Read the command byte and throw away.
				SERIAL.read();
				// Turn off torch up for test
				digitalWrite(OUT_D_TORCH_UP, OUT_D_TORCH_UP_NOT_ACTIVE);
				break;

			case PC_CMD_TEST_THC_DOWN_ON:
				// Read the command byte and throw away.
				SERIAL.read();
				// Turn on torch down for test
				digitalWrite(OUT_D_TORCH_DOWN, OUT_D_TORCH_DOWN_ACTIVE);
				break;

			case PC_CMD_TEST_THC_DOWN_OFF:
				// Read the command byte and throw away.
				SERIAL.read();
				// Turn off torch down for test
				digitalWrite(OUT_D_TORCH_DOWN, OUT_D_TORCH_DOWN_NOT_ACTIVE);
				break;

                        case PC_SET_COUNT_ON_HYSTERISIS:
                               break;
                               
                        case PC_SET_COUNT_OFF_HYSTERISIS:
                               break;
                               
                        case PC_SET_TORCH_STABILIZE_MILLISEC:
                               break;
                               
                        // Consider adding messages to set kerf threasdhold values.
                               

			default:
				break;
			}
		}

		//
		// RUN THE STATE MACHINE
		//

		// If in Disabled mode, don't do anything.
		if (currentStateData.currentMode == THC_MODE_DISABLED)
		{
			// Nothing is done when disabled.

			// Only update the display about 4 times a second (assuming a 1 ms loop time).
			if (++displayUpdateDelay > 250)
			{
				sendFullVoltageMessage();
				displayUpdateDelay = 0;
			}
		}
		// If in Bypass mode, use the handler that just passes signals through.
		else if (currentStateData.currentMode == THC_MODE_BYPASS)
		{
			//bypassHandler->controlLoop();

			// Only update the display about 4 times a second (assuming a 1 ms loop time).
			if (++displayUpdateDelay > 250)
			{
				sendFullVoltageMessage();
				displayUpdateDelay = 0;
			}

		}
		// If in Cruise mode, used the handler that just passes through
		// until the user hits the "Select" button to start the THC function.
		else if (currentStateData.currentMode == THC_MODE_CRUISE)
		{
			//bypassHandler->controlLoop();

			// Only update the display about 4 times a second (assuming a 1 ms loop time).
			if (++displayUpdateDelay > 250)
			{
				sendFullVoltageMessage();
				displayUpdateDelay = 0;
			}
		}
		// In the Enabled mode, do the standard full height control processing.
		else if (currentStateData.currentMode == THC_MODE_OPERATING)
		{
			//
			// RUN THE APPRORIATE HANDLER BASED ON THE STATE
			//

			// Run the state handler based on the current state,
			// either Enabled (waiting to cut) or cutting.
			if (currentStateData.currentState == THC_STATE_ENABLED)
			{
				// Enabled state handler returns true if usage data should be saved.
				if (StateEnabledHandler())
				{
					// Copy the updated data to the flash object
					//usageData.voltSetPoint = currentStateData.voltSetPoint;
					flash.DataSetAll((THCStatData *) &usageData);
					// Write the object data to the memory.
					flash.DataSave();
					// Clear the new data flag.
					currentStateData.usageUpdated = false;
					usageData.initialWriteCount++;
				}

      			    // Only update the display about 4 times a second (assuming a 1 ms loop time).
  			    if (++displayUpdateDelay > 250)
  			        {
    				  sendFullVoltageMessage();
  				  displayUpdateDelay = 0;
  			        }
			}

			else if (currentStateData.currentState == THC_STATE_CUTTING)
			{
				StateCuttingHandler();
                                if (captureOn)
                                  {
                                    sendFullVoltageMessage();
                                  }
			}



		} // State handler
	}  // While (1)

}	// loop()





void TestTorchOn(bool value)
{
	if (value)
		// Turn on torch for test
		digitalWrite(OUT_D_TORCH_RELAY, OUT_D_TORCH_RELAY_ACTIVE);
	else
		// Turn off torch for test
		digitalWrite(OUT_D_TORCH_RELAY, OUT_D_TORCH_RELAY_NOT_ACTIVE);

}

#if NOPE
// Check for keypress to start controlling cutting.
if (display.processCruiseButtons() == COMMAND_CRUISE_SET)
{
	if ( currentStateData.torchOnState && currentStateData.arcGoodState &&
			(currentStateData.currentVoltage > MIN_CRUISE_SET_VOLTAGE))
	{
		display.setMenu(MENU_OPERATING);
		//currentStateData.voltSetPoint = currentStateData.currentVoltage;
		currentStateData.currentMode = THC_MODE_ENABLED;
		currentStateData.currentState = THC_STATE_CUTTING;
		currentStateData.runVoltageControl = true;
	}
}
}
#endif

#if NOPE
void processCommand(Command_e newCmd)
{
// Process any command returned by the state handler.
switch (newCmd)
{
	default:
	case COMMAND_NONE:
	//SERIAL.print("COMMAND_NONE\n");
	break;

	case COMMAND_VOLT_UP:
	DebugPrint("COMMAND_VOLT_UP\n");
	if (currentStateData.voltSetPoint < 999)
	{
		usageData.voltSetPoint = ++currentStateData.voltSetPoint;
		// Start timer for delayed memory write
		currentStateData.lastUseTimer.startTimer();
		currentStateData.usageUpdated = true;
	}
	break;

	case COMMAND_VOLT_DOWN:
	DebugPrint("COMMAND_VOLT_DOWN\n");
	if (currentStateData.voltSetPoint > 25)
	{
		usageData.voltSetPoint = --currentStateData.voltSetPoint;
		// Start timer for delayed memory write
		currentStateData.lastUseTimer.startTimer();
		currentStateData.usageUpdated = true;
	}
	break;

	case COMMAND_CALIBRATE_VOLTAGE:
	DebugPrint("COMMAND_CALIBRATE_VOLTAGE\n");
	break;

	case COMMAND_RESET_USE_DATA:
	DebugPrint("COMMAND_RESET_USE_DATA\n");
	// Reset the usage data.
	flash.DataReset();
	// Reload the reset values.
	flash.DataGetAll((THCStatData*) &usageData);
	break;

	case COMMAND_RESET_FLASH_BLOCK:
	DebugPrint("COMMAND_RESET_FLASH_BLOCK\n");
	// Set the flash block to the next block after the current and
	// update the program variable with the block reference.
	usageData.flashBlock = flash.setBlock(flash.getBlock() + 1);
	// Flush all the usage data to the flash variables
	flash.DataSetAll((THCStatData*) &usageData);
	// Save the current usages to the new block.
	flash.DataSave();
	break;

	case COMMAND_SAVE_USAGE_DATA:
	// Copy the updated data to the flash object
	//usageData.voltSetPoint = currentStateData.voltSetPoint;
	flash.DataSetAll((THCStatData *) &usageData);
	// Write the object data to the memory.
	flash.DataSave();
	// Clear the new data flag.
	currentStateData.usageUpdated = false;
	usageData.initialWriteCount++;
	break;

}

}

#endif

#ifdef NOPE
// Only update the display about 20 times a second (assuming a 1 ms loop time).
//		if (++delayDisplayUpdate > 5)
{
sendFullVoltageMessage();
delayDisplayUpdate = 0;
}
#endif

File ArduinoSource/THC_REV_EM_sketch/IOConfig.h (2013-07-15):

/*
* COPYRIGHT 2013 - Regis M. George
 *
 * License: Creative Commons Attribution-NonCommercial-ShareAlike 3.0 Unported License
 *
*/

/*
 * IOConfig.h
 *
 *  Created on: Sep 23, 2012
 *      Author: Rege
 */

#ifndef IO_CONFIG_H_
#define IO_CONFIG_H_

#include "Platform.h"

//
// DIGITAL INPUTS
//

// INPUTS - FROM CNC
// Define the pin for the torch on request
// from the CNC
#ifdef MICRO_THC
#define IN_D_TORCH_ON_PIN      6
#else
#define IN_D_TORCH_ON_PIN      10
#endif

// INPUTS - FROM PLASMA
// Define the pin for the arc okay signal
// from the plasma
#ifdef MICRO_THC
#define IN_D_ARC_GOOD_PIN 	8
#else
#define IN_D_ARC_GOOD_PIN 	12
#endif

//
// DIGITAL OUTPUTS
//

// OUTPUTS - TO CNC
#ifdef MICRO_THC
#define OUT_D_ARC_GOOD 		3
#define OUT_D_TORCH_UP 		2
#define OUT_D_TORCH_DOWN	4
#else
#define OUT_D_ARC_GOOD 		2
#define OUT_D_TORCH_UP 		3
#define OUT_D_TORCH_DOWN	4
#endif

// OUTPUTS - TO PLASMA
// Output to trip relay to turn on torch
#ifdef MICRO_THC
#define OUT_D_TORCH_RELAY	7
#else
#define OUT_D_TORCH_RELAY	11
#endif


#define IN_D_TORCH_ON_PIN_ACTIVE 	LOW
#define IN_D_ARC_GOOD_PIN_ACTIVE 	LOW

//
// Use macros to define active high or low for
// each of the output pins.
//
#define OUT_D_ARC_GOOD_ACTIVE			LOW
#define OUT_D_ARC_GOOD_NOT_ACTIVE		HIGH
#define OUT_D_TORCH_UP_ACTIVE			LOW
#define OUT_D_TORCH_UP_NOT_ACTIVE		HIGH
#define OUT_D_TORCH_DOWN_ACTIVE			LOW
#define OUT_D_TORCH_DOWN_NOT_ACTIVE		HIGH
#define OUT_D_TORCH_RELAY_ACTIVE		HIGH
#define OUT_D_TORCH_RELAY_NOT_ACTIVE	        LOW

//
// ANALOG I/O
//

// Define the analog in for torch voltage sensing.
#ifdef MICRO_THC
#define IN_A_VOLTAGE A1
#else
#define IN_A_VOLTAGE A0
#endif
#endif /* IO_CONFIG_H_ */

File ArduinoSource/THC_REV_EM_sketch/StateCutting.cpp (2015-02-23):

/*
* COPYRIGHT 2013 - Regis M. George
 *
 * License: Creative Commons Attribution-NonCommercial-ShareAlike 3.0 Unported License
 *
*/

/*
* COPYRIGHT 2013 - Regis M. George
 *
 * License: Creative Commons Attribution-NonCommercial-ShareAlike 3.0 Unported License
 *
*/

/*
 * StateCutting.cpp
 *
 *  Created on: Oct 15, 2012
 *      Author: Rege
 */
#include "THC.h"

#include "IOConfig.h"
#include "Timer.h"
#include "Messages.h"

#include "StateCutting.h"

// 5 volts (35 counts) is the immediate threshold.
#define KERF_ENCOUNTERED_THRESHOLD (currentStateData.voltSetPoint + (35))
#define KERF_ENCOUNTERED_DELAYED_THRESHOLD (currentStateData.voltSetPoint + (VOLTAGE_ON_HYSTERESIS*2))
#define KERF_CLEARED_THRESHOLD (currentStateData.voltSetPoint + (VOLTAGE_ON_HYSTERESIS*2))



void TorchUp()
	{
	// Turn on TorchUp
	digitalWrite(OUT_D_TORCH_UP, OUT_D_TORCH_UP_ACTIVE);
	// Make sure TorchDown is off
	digitalWrite(OUT_D_TORCH_DOWN, OUT_D_TORCH_DOWN_NOT_ACTIVE);
	// Set the flags for torch status.
	currentStateData.torchDown = false;
	currentStateData.torchUp = true;
	}




void TorchDown()
	{
	// Make sure TorchUp is off
	digitalWrite(OUT_D_TORCH_UP, OUT_D_TORCH_UP_NOT_ACTIVE);
	// Turn on TorchDown
	digitalWrite(OUT_D_TORCH_DOWN, OUT_D_TORCH_DOWN_ACTIVE);
	// Set the flags for torch status.
	currentStateData.torchDown = true;
	currentStateData.torchUp = false;
        // Start the kerf timer.
        currentStateData.kerfTimer.startTimer();
	}




void TorchKerf()
	{
	// Make sure TorchUp is off
	digitalWrite(OUT_D_TORCH_UP, !OUT_D_TORCH_UP_ACTIVE);
	// Make sure TorchDown is off
	digitalWrite(OUT_D_TORCH_DOWN, !OUT_D_TORCH_DOWN_ACTIVE);
	// Set the flags for torch status.
	currentStateData.torchDown = false;
	currentStateData.torchUp = false;
	currentStateData.kerfEncountered = true;
	currentStateData.runVoltageControl = false;
	}




void TorchKerfCrossed()
	{
	currentStateData.kerfEncountered = false;
	currentStateData.runVoltageControl = true;
	}




void TorchGood()
	{
	// Make sure TorchUp is off
	digitalWrite(OUT_D_TORCH_UP, !OUT_D_TORCH_UP_ACTIVE);
	// Make sure TorchDown is off
	digitalWrite(OUT_D_TORCH_DOWN, OUT_D_TORCH_DOWN_NOT_ACTIVE);
	// Set the flags for torch status.
	currentStateData.torchDown = false;
	currentStateData.torchUp = false;
	currentStateData.kerfEncountered = false;
	currentStateData.runVoltageControl = true;
	}


void SignalUpdateForTorchOrArcOff()
	{
	// Make sure TorchUp is off
	digitalWrite(OUT_D_TORCH_UP, !OUT_D_TORCH_UP_ACTIVE);
	// Make sure TorchDown is off
	digitalWrite(OUT_D_TORCH_DOWN, OUT_D_TORCH_DOWN_NOT_ACTIVE);
	// Set the flags for torch status.
	currentStateData.torchDown = false;
	currentStateData.torchUp = false;
	currentStateData.kerfEncountered = false;
	currentStateData.runVoltageControl = false;
	}


void StateCuttingHandler()
	{
        int cutVoltDelta;
        
	//
	// Check for ARC GOOD changes
	//

	// See if the Arc Ok signal changed so display can be updated.
	if (currentStateData.arcStateChanged)
		{
		// Clear the flag to denote we handled the state update.
		currentStateData.arcStateChanged = false;
		// If the arc good went on, update the usage data.
		if (currentStateData.arcGoodState)
			{
			// Update the pierce count since we finished a pierce.
			usageData.pierceCount++;
			// Update the flag so the data will be flushed later.
			currentStateData.usageUpdated = true;
			// Start the timer that tracks torch on time.
			currentStateData.torchOnTimer.startTimer();
			}
		}

	//
	// Check for the TORCH ON signal being turned off.
	//
	if (!currentStateData.torchOnState)
		{
		// Turn off the relay so that the torch on signal to the plasma goes off.
		digitalWrite(OUT_D_TORCH_RELAY, OUT_D_TORCH_RELAY_NOT_ACTIVE);
		// Must ensure torch up/down off if torch off.
                SignalUpdateForTorchOrArcOff();

		// Change the state from cutting to enabled.
		currentStateData.currentState = THC_STATE_ENABLED;

		// Start timer for delayed memory write
		currentStateData.lastUseTimer.startTimer();

                // Update the mode display
                SendMode();

		// Return now with no new command to process.
		return;
		}

	//
	// Check for the arc going out.
	//
	if (!currentStateData.arcGoodState)
		{
		// Reset control flags
                SignalUpdateForTorchOrArcOff();
		return;
		}

	//
	// If voltage control is not active, see if it should be turned on.
	//
	if (!currentStateData.runVoltageControl)
		{
		// Handle the case where voltage control is off due to a kerf being crossed.
		if (currentStateData.kerfEncountered)
                    {
                     if (currentStateData.currentVoltage <= (currentStateData.voltSetPoint + (2 * VOLTAGE_ON_HYSTERESIS)) )
                        // Turn voltage control back on
                        // Set flag to "no kerf"
                        TorchKerfCrossed();
                     else
                       // Still in the kerf, so don't do anything.
                       return;
                    }

		// This is the initial start of cut case, so see if the timer has expired.
		else if (currentStateData.torchStabilizeTimer.elapsedMilliSeconds() > TORCH_STABILIZE_TIME_MLLISECONDS)
			{
			currentStateData.runVoltageControl = true;
			}
                else
        	   // Thre is no need to do voltage control at this time.
        	   return;
		}


	//
	// Run the voltage control.
	//

	// One of the following is done:
	//	1) See if the voltage is too low, and if so turn on Torch Up
	//	1) if Torch is going Up, see if high enough and turn off if needed
	//	2) a) if Torch is going Down, see if low enough and turn off if needed
	//     b) see if we're crossing a kerf, and if so, turn off voltage control
	//	4) See if the voltage is too high, and if so turn on Torch Down
	//
	// After torch height control is done, see if the user it trying to
	// adjust the tip voltage.

	//
	// Handle case of where Torch Up is active
	//
	if (currentStateData.torchUp)
		{
		// Check to see if the torch is high enough.
		if (currentStateData.currentVoltage >=
			(currentStateData.voltSetPoint - VOLTAGE_OFF_HYSTERESIS))
			{
			// Handle case of torch at height.
			TorchGood();
			}
		}

	//
	// See if the voltage is too low, and if so, move the torch up.
	//
	else if (currentStateData.currentVoltage <=
			(currentStateData.voltSetPoint - VOLTAGE_ON_HYSTERESIS))
		// Update display that torch needs to go up
		TorchUp();

	//
	// Handle the case where Torch Down is active
	//
	else if (currentStateData.torchDown)
		{
		// Check to see if the torch is low enough.
		if (currentStateData.currentVoltage <=
			(currentStateData.voltSetPoint + VOLTAGE_OFF_HYSTERESIS))
			{
			// Handle case of torch at height.
			TorchGood();
			}
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

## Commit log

2013-02-10 Rev 0.e - fully functional on modified Rev A board.
    [THC-schematic.brd, THC-schematic.sch]
2013-04-02 Rev C Hardware
    [THC-schematic.brd, THC-schematic.sch]
2013-07-15 Updated all files for Rev E-Shield and Rev E-Micro.
    [THC-schematic.brd, THC-schematic.sch, THC-schematicRevE.brd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]
2013-07-20 Updated manual to include Micro white wires, BOM, schematics/layouts.
2013-07-22 Added section to manual for programming the Arduino. Cleaned up schematic files.
    [THC-schematicRevEM.brd, THC-schematicRevEM.sch, THC-schematicRevEM2.brd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]
2013-11-23 Fixed issue with kerf detection. Don't know what changed to break it.
    [StateCutting.cpp, THC.h]
2015-02-23 Working files (old updates). I think this is the "fixed" Mach plug-in.
    [StateCutting.cpp, THC.h, THC_REV_EM_sketch.ino]
2015-02-24 Release files have the most current DLL build.
